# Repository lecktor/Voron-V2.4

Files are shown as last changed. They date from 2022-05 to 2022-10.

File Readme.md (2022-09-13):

# Voron V2.4R2 Kit by Lecktor

Lecktor.com sells full solution kit. To get a better understanding, please
take a look at our [manuals](./Manuals/Readme.md). For whats included in kit and why, take a look at mods like [NeverMore](./NeverMore/Readme.md), [EuclidProbe](./EuclidProbe/Readme.md), [Titanium Backers](./Backers/Readme.md), [Microswitch Endstop](./Microswitch_Endstop/Readme.md), [Door Hinges](./Door_Hinges/Readme.md) and other folders for more information. 

# Full BOM of kit
## Frame kit
- LDO Motors frame kit (black) - 1pcs

## Motor kit
- LDO Motors LDO-42STH48-2004AC (Z motor) - 4pcs
- LDO Motors LDO-42STH48-2004MAH (AB motor) - 2pcs
- LDO Motors LDO-36STH20-1004AHG (E motor) - 1pcs

## Linear rail kit
### Voron V2.4 250x250
- Linear rail LDO-SLR9H-300Z0 (stainless steel)  - 6pcs
- Linear rail LDO-SLR12H-300Z1 (stainless steel) - 1pcs
### Voron V2.4 300x300
- Linear rail LDO-SLR9H-350Z0 (stainless steel)  - 6pcs
- Linear rail LDO-SLR12H-350Z1 (stainless steel) - 1pcs
### Voron V2.4 350x350
- Linear rail LDO-SLR9H-400Z0 (stainless steel)  - 6pcs
- Linear rail LDO-SLR12H-400Z1 (stainless steel) - 1pcs

## Motion kit
- RainDew F695-2RS flanged bearing  (ABEC-7) - 20pcs
- RainDew 625-2RS ball bearing (ABEC-7) - 12pcs
- Runice pulley 16T/6mm/5mm (black) - 4pcs
- Runice pulley 20T/6mm/5mm (black) - 2pcs
- Runice pulley 20T/9mm/5mm (black) - 4pcs
- Runice pulley 80T/6mm/5mm (black) - 4pcs
- Runice idler 20T/6mm/5mm (black) - 2pcs
- Runice idler 20T/9mm/5mm (black) - 4pcs
- Gates Unitta belt loop 188-2GT-6RF - 4pcs
- Shaft 5x61mm - 4pcs
### Voron V2.4 250x250
- Gates Unitta timing belt LL-2GT-9RF (910mm)  - 4pcs
- Gates Unitta timing belt LL-2GT-6RF (1600mm) - 2pcs
### Voron V2.4 300x300
- Gates Unitta timing belt LL-2GT-9RF (1010mm) - 4pcs
- Gates Unitta timing belt LL-2GT-6RF (1800mm) - 2pcs
### Voron V2.4 350x350
- Gates Unitta timing belt LL-2GT-9RF (1110mm) - 4pcs
- Gates Unitta timing belt LL-2GT-6RF (2000mm) - 2pcs

## BuildPlate kit
### Voron V2.4 250x250
- LDO Motors spring steel sheet (textured; 254x254x0.5mm) - 1pcs
- Schallenkammer magnetic foil (graviflex; 255x255x1mm) - 1pcs
- Lecktor universal build plate (250x250x8mm) - 1pcs
- Keenovo heating pad (200x200mm; 500W/220V) - 1pcs
### Voron V2.4 300x300
- LDO Motors spring steel sheet (textured; 305x305x0.5mm) - 1pcs
- Schallenkammer magnetic foil (graviflex; 305x305x1mm) - 1pcs
- Lecktor universal build plate (300x300x8mm) - 1pcs
- Keenovo heating pad (240x240mm; 600W/220V) - 1pcs
### Voron V2.4 350x350
- LDO Motors spring steel sheet (textured; 355x355x0.4mm) - 1pcs
- Schallenkammer magnetic foil (graviflex; 355x355x1mm) - 1pcs
- Lecktor universal build plate (350x350x8mm) - 1pcs
- Keenovo heating pad (300x300mm; 750W/220V) - 1pcs

## Panels kit
- Lecktor (NeoBond 4mm/black; PMMA 3mm/clear) - 1pcs

## Chains set
### Voron V2.4 250x250
- Igus E2i.10.10.018.0 energy chain (16 links) - 2pcs
- Igus E2.15.10.028.0 energy chain (22 links) - 1pcs
### Voron V2.4 300x300
- Igus E2i.10.10.018.0 energy chain (19 links) - 2pcs
- Igus E2.15.10.028.0 energy chain (25 links) - 1pcs
### Voron V2.4 350x350
- Igus E2i.10.10.018.0 energy chain (22 links) - 2pcs
- Igus E2.15.10.028.0 energy chain (28 links) - 1pcs

## Electronics kit
- Fysetc Spider 446 V2.2 - 1pcs
- Fysetc TMC2209 V3.1 - 7pcs
- Fysetc Mini12864 RGB LCD V2.1 (type B) - 1pcs
- Raspberry PI 4 Model B (4Gb) - 1pcs
- Fisher Elektronik heatsink for Raspberry PI (ICK BGA; 14x14x10mm) - 1pcs
- 3M heat transfer tape (3M 8810; 15x15x0.25mm) - 1pcs
- Goodram 16Gb memmory card - 1pcs
- Sunon axial fan (MF60202V3-1000U-A99) - 2pcs
- Lecktor microswitch endstop module (black; PCB) - 1pcs
- Lecktor Z-endstop (black; PCB assembly) - 1pcs

## Power kit
- MeanWell RSP-200-24 PSU - 1pcs
- MeanWell RS-25-5 PSU - 1pcs
- Omron SSR G3NA-210B-UTU 5-24VDC - 1pcs
- SSR DIN rail mounting bracket (R99-12; black) - 1pcs
- ZF Electronics rocker switch DPST 16A (WRG32F2BBRLN) - 1pcs
- TE Connectivity power inlet 10EGG1-2 - 1pcs
- LittleFuse 0232004.MXP - 2pcs
- Logilink keystone CAT6 insert (shielded; NK4011) - 1pcs
- Logilink patch cord (black; 1m) - 1pcs
- ESPE IEC C13 power cable (black; 1.5m) - 1pcs
- Schneider Electric terminal block 2.5mm2 NSYTRV22 (grey) - 2pcs
- Schneider Electric terminal block 2.5mm2 NSYTRV22BL (blue) - 2pcs
- Schneider Electric terminal block 2.5mm2 NSYTRV22PE (ko-ro) - 2pcs
- Schneider Electric terminal cover 2.5mm2 NSYTRAC22 - 1pcs
- Schneider Electric bridge 2.5mm2 NSYTRAL22 - 3pcs
- OBO wiring box 40Kx25L LK4 40025 (gray; PVC) - 1pcs

## Wire harness kit
- Lecktor stealhburner wire harness (Heluflon; JST; Molex) - 1pcs
- Lecktor power line wire harness (Heluflon) - 1pcs
- Lecktor miscellaneous wire harness (Heluflon; JST; Molex) - 1pcs

## Toolhead kit
- Phaetus Dragon hotend (black; HF) - 1pcs
- Phaetus Dragon silicone sock (black) - 1pcs
- Phaetus heater cartridge (24V/50W) - 1pcs
- Phaetus thermistor cartridge (104NT-4-R025H42G) - 1pcs
- Bondtech drivegear kit 1.75/5.0 - 1pcs
- Bondtech shaft assembly - 1pcs
- Bondtech thumbscrew assembly - 1pcs
- RainDew ball bearing MR85ZZ - 2pcs
- GDSTime axial fan (4010; 24V) - 1pcs
- Delta Electronics blower fan (5015; 24V) - 1pcs
- Lecktor toolhead front (Dragon/CW2/Nylon/MJF; black) - 1pcs
- Lecktor toolhead rear (Dragon/CW2/Nylon/MJF; black) - 1pcs

## Hardware kit
- Lecktor hardware kit (black) - 1pcs
- LDO Motors Voron V2.4 t-nuts - 1pcs
- LDO Motors Voron V2.4R2 rubber feet - 4pcs
- Lecktor hammer head M3 nuts (100pcs) - 1pcs

## DIN rails
### Voron V2.4 250x250
- Lecktor DIN rail (35x7.5x368mm; zinc) - 2pcs
### Voron V2.4 300x300
- Lecktor DIN rail (35x7.5x418mm; zinc) - 2pcs
### Voron V2.4 350x350
- Lecktor DIN rail (35x7.5x468mm; zinc) - 2pcs

## Miscellaneous
- Misumi extrusion slot cover (black; 1m) - 1pcs
- Foam panel tape (1x5x2000mm) - 2pcs
- Foam panel tape (3x5x3000mm) - 2pcs
- 3M VHB 5952 (9x5.5x2500mm) - 1pcs
- Bowden coupler (black; 4mm) - 1pcs
- PTFE tube (black; 4x2x1000mm) - 1pcs
- Neodymium disc magnet (black; 6x3mm) - 10pcs
- KSS Wiring cable tie (Polyamide; 1.6x71mm; black) - 100pcs
- FIX&FASTEN cable tie (Polyamide; 2.5x150mm; black) - 100pcs
- Misumi HNTAJ5-3 nut - 10pcs
- Misumi HNTAJ5-5 nut - 10pcs
- Cable duct for rails - 4pcs
- Cable sleeves for bottom - 3pcs

## LED mounts
- BTF-Lightning SK6812 led strip (250-350mm) - 3pcs
- FIX&FASTEN led profile (9.30x16x250-350mm) - 3pcs
- LED mounts plastic parts (eSun ABS+; black) - 6pcs
- LED mounts wire harness - 1pcs

## Titanium backers
- Lecktor Titanium backers hardware kit - 1pcs
### Voron V2.4 250x250
- LWLW X-rail backer (Titanium grade 2; 2x18x260mm) - 2pcs
- LWLW Y-rail backer (Titanium grade 2; 3x18x290mm) - 1pcs
### Voron V2.4 300x300
- LWLW X-rail backer (Titanium grade 2; 2x18x310mm) - 2pcs
- LWLW Y-rail backer (Titanium grade 2; 3x18x340mm) - 1pcs
### Voron V2.4 350x350
- LWLW X-rail backer (Titanium grade 2; 2x18x360mm) - 2pcs
- LWLW Y-rail backer (Titanium grade 2; 3x18x390mm) - 1pcs

## Nevermore assembly
- Nevermore carbon bag - 1pcs
- Sunon blower fan (MF5015VX-00U-A99; 12V) - 2pcs
- Lecktor Nevermore hardware kit (black) - 1pcs
- Lecktor Nevermore wire harness (Heluflon; JST) - 1pcs
- Lecktor Nevermore plastic parts (ABS GF; black) - 1pcs

## Euclid probe assembly
- Lecktor Euclid PCB assembly - 1pcs  
~~Lecktor Euclid wire harness (Heluflon; JST) - 1pcs~~  
~~Lecktor Euclid plastic parts (ABS GF; black) - 1pcs~~  
  
## Voron V2.4R2 plastic parts
- Main functional parts (eSun ABS+; black) - 1pcs
- Accent functional parts (eSun ABS+; red/gold) - 1pcs
- Skirts (eSun ABS+; black/red/gold) - 1pcs
- All threaded inserts are installed

###### Tags: V2.4, 2.4, V2.4R2, V2.4 R2

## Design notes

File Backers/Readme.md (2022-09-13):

# Gantry Backing Plates

## The theory
Due to different thermal coefficients of linear expansion between steel (rails) and aluminum (extrusions), the Voron V2 gantry forms a sort of giant bimetal temperature sensor element. This causes a warping of the gantry as it heats up with increasing chamber temperature.

## The evidence
While exploring [frame expansion behavior](https://github.com/tanaes/whopping_Voron_mods/tree/main/docs/frame_expansion), a number of us were noticing empirical values several times what we'd predict simply due to linear expansion of the Z extrusions alone. Although plugging those empirical values in to the compensation code has given me great first layers, the difference from expectation was still bothering me. Maybe, I thought, there was some sort of warping happening? Checking out a table of thermal expansion coefficients, I saw that indeed aluminum expands quite a bit more than steel with temperature.

### Bottom X rail increases frame thermal compensation value

After some discussion on Discord, it appeared that people running the BOM double X rail, with an MGN9 rail on the front and bottom of the X extrusion, by and large seemed to be needing higher compensation values than those who only had a single X rail on the front face of the extrusion.

So I tried loosening the screws on the bottom X rail of my V2.4 350, and re-ran the thermal expansion measurment. Wouldn't you know it, my observed compensation factor went from around 2.8 to about 1.5:

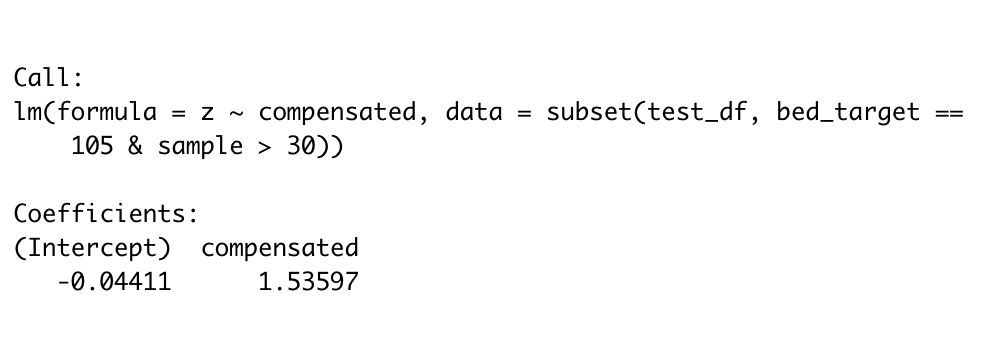
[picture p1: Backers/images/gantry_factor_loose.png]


### Bed mesh changes as predicted with frame temperature

To confirm, I decided to go ahead an loosen *all* the rails on both X and Y, heat soak the machine for a couple hours, and then tighten them down; this should ensure that the gantry is as flat as possible when at temperature, but will bow downwards when it is cold as the aluminum contracts more than the steel rail beneath.

And that's indeed what I saw. After hot-tightening the rails, I took a bed mesh while everything was still hot. I then allowed the printer to cool for a couple hours, reheated the bed, and took another mesh while the bed was hot but the frame was still cold.

What I saw was just what we'd predict, with the "hot frame" measurement (left) being quite flat, but the "cold frame" measurement appearing as if the center of the bed were closer to the probe:

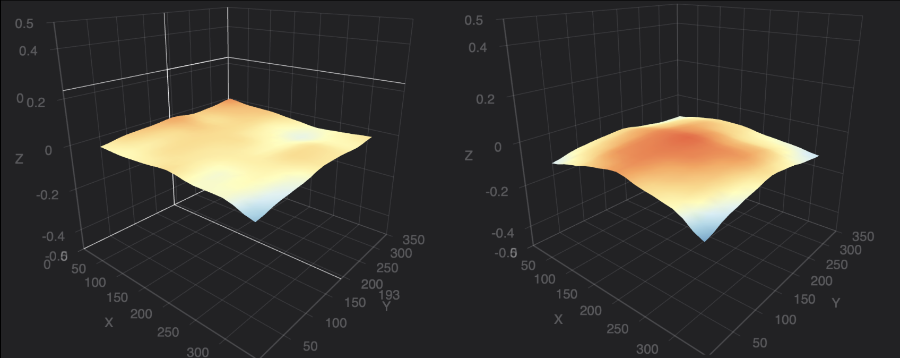
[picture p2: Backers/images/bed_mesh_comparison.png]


### Shitty modeling is consistent with observation

Finally, I put together a *very simplistic* FEA model in Fusion360. It did the thing with the bendy bendy:

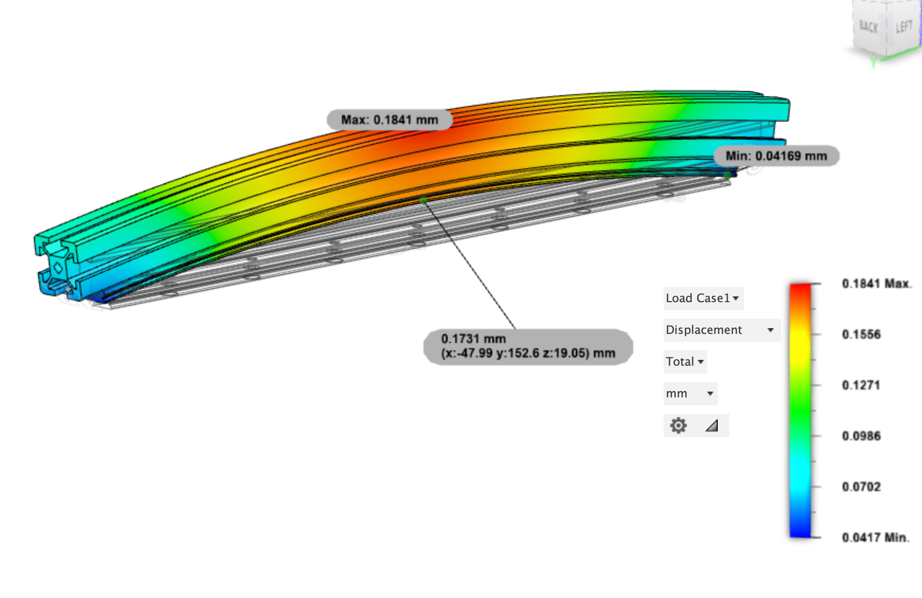
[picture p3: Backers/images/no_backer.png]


 ***Caveat: I am a biologist, not an engineer!*** I only barely know what I'm doing with this shit. But with the rail material set to 440C stainless and the extrusion to 6061 aluminum, with them bonded at the interface, a temperature delta of 40° C led to this 250mm-sized X gantry member deflecting 0.17 mm upwards in the center! That's definitely not trivial, and it's certainly consistent with our empirical observations.
 
## The (a) solution (maybe??)
 
Why have *bi*metal when you can have *tri*metal?!

At one extreme, bolting another MGN9 rail on top of the extrusion seems certain to cancel out the bending moment imparted by the one on the bottom. 

As a cheaper alternative, I've designed some laser-cut steel extrusion backing plates that weigh less and are lower-profile than rails, but which should at least do a reasonable job at counteracting the thermal defection.

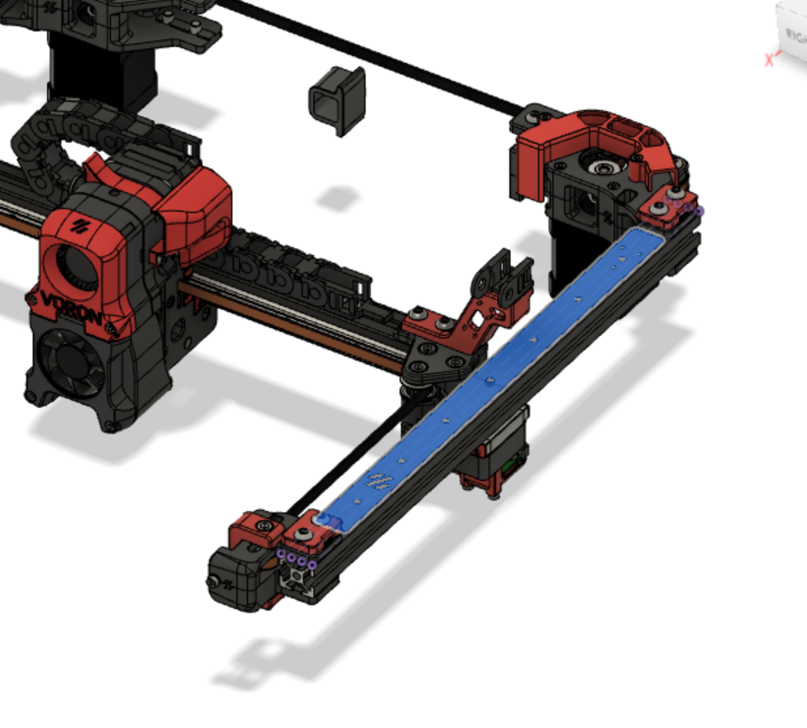
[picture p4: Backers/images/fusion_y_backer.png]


These are sized to fit along the top of the Y extrusion and on the top or back of the X extrusion, with a few mm of clearance to printed endpieces:

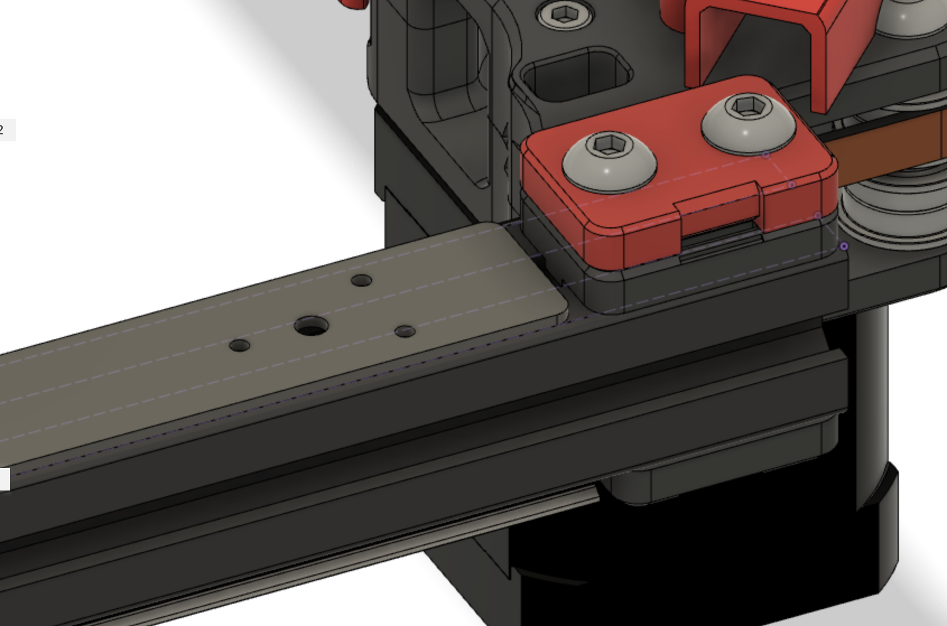
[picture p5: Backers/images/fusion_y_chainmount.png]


They also have pilot holes for the cable chain end link to attach. They are sized to be drilled out with a 2.5 mm bit and then M3 tapped. (Laser cutting hardens the steel at the cut, so the cut holes are undersized for drilling out to be a bit gentler on your taps.)

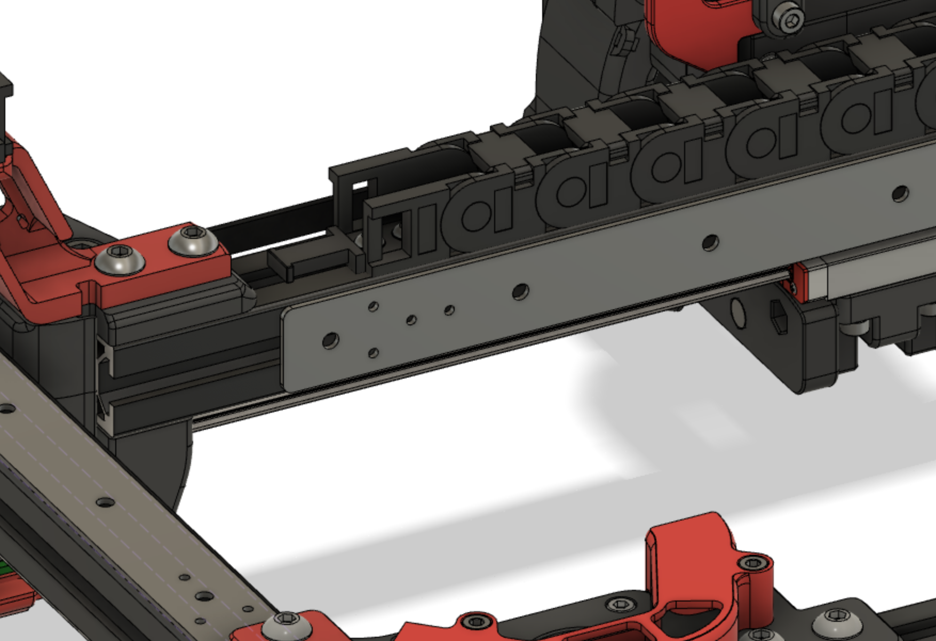
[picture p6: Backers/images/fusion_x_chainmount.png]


To attach them most optimally, you'll also need to countersink the holes so they can be installed with 6mm flat head M3 screws.

### Simulation results

Plugging these into the FEA model shows some serious improvements with a 1.9 mm steel backer:

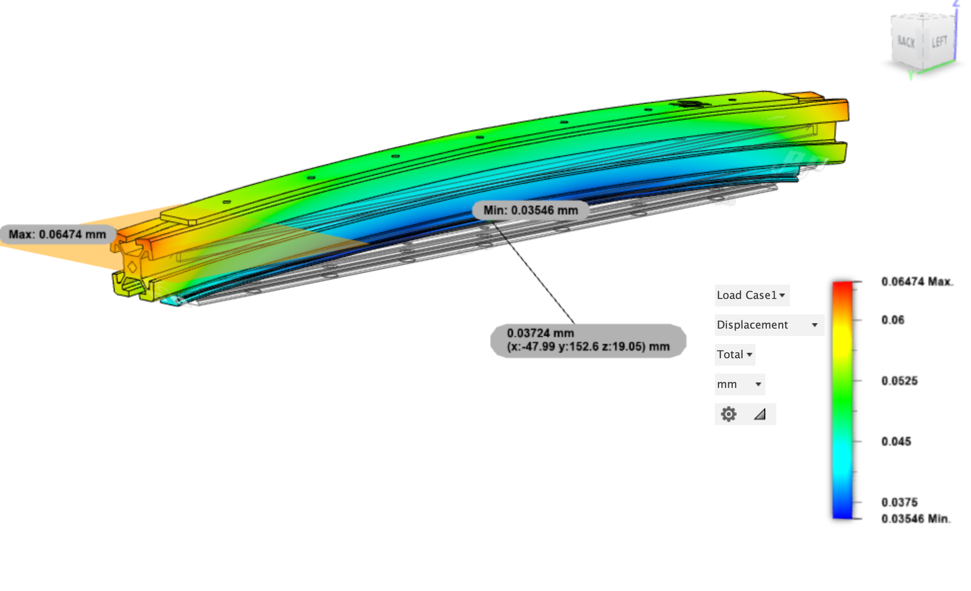
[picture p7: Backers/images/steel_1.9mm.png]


A 1.5 mm titanium backer does even better:

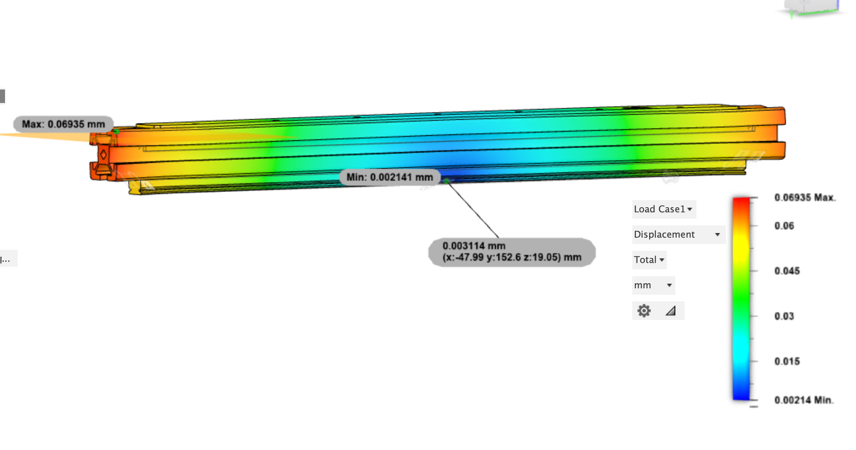
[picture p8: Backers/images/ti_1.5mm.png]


### Sourcing

A set of 3 backers in 1.9 mm steel can be bought at [SendCutSend](https://www.sendcutsend.com) for somewhere in the neighborhood of $10 (presuming you've met their minimum order of $29). 

If you're feeling spendy, even the Ti backers still cost about the same as cheapo linear rails, with a set of three costing around $60.

## The results

I put in an order for 8 sets of backers in various sizes, all of which have been sent out to people on the Voron Discord for testing. Most of these were in mild steel, but there are also a few pieces in titanium.

Results from testing are below.

### Case study 1: whoppingpochard, steel backers X and Y

After countersinking and tapping my mild steel backers, I tried hastily cold-bluing them with some gun blue. The results were decidedly mixed, and I *also* very conveniently misplaced my 3-in-1, so sadly they were a little splotchy the next morning. They installed perfectly on the machine, though, with apparently just enough clearance without modifying cable chains: 

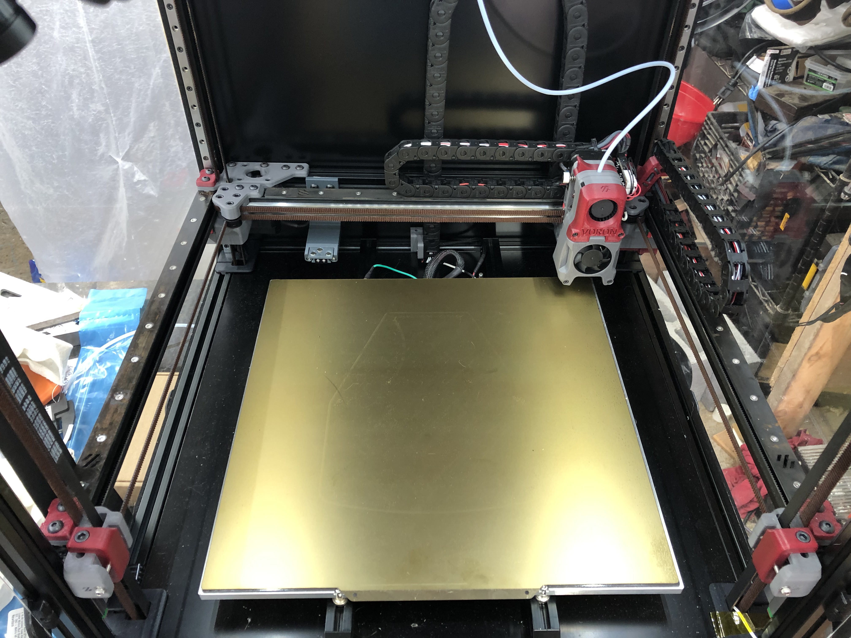
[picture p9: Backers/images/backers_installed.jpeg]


To test, I performed the following operation:
1. preheated the bed
2. took a bed mesh while bed was still hot
3. took a bed mesh after 2 hour heat soak (frame at ~35° C)
4. installed backers on each axis
5. repeated steps 1-3

This is the result:

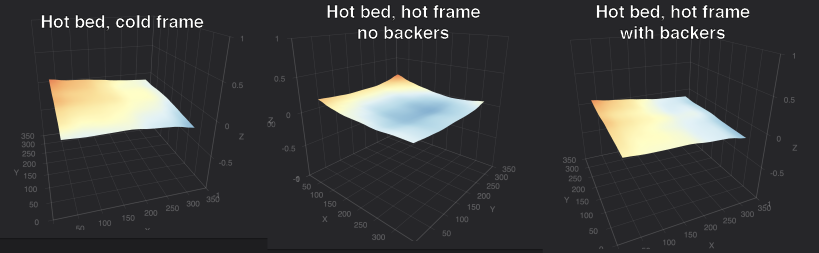
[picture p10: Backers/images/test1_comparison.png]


(Please ignore the odd tilt of the bed, as I think I did QGL at a non-equilibrium point.)

The hot bed appears pretty planar from the perspective of the toolhead while the frame is still cold. *Without* backers, after the frame has heatsoaked, the bed appears cupped -- presumably due to the extrusion bending upward towards the center. 

But *with* backers installed, the bed still appears planar after the heatsoak. This appears to indicate the backers are actually working!

I also developed a script to test gantry bowing in a more controlled fashion. Essentially, the script does a bed mesh while the frame is cold and then another once the frame heats up, and compares the two. As long as the bed is the same temperature for each mesh, we assume that any non-linear deviation measured is a result of flexing frame members.

Here are the results from my printer, with and without backers installed (I ran this test after swapping out the steel X backer for a titanium one):

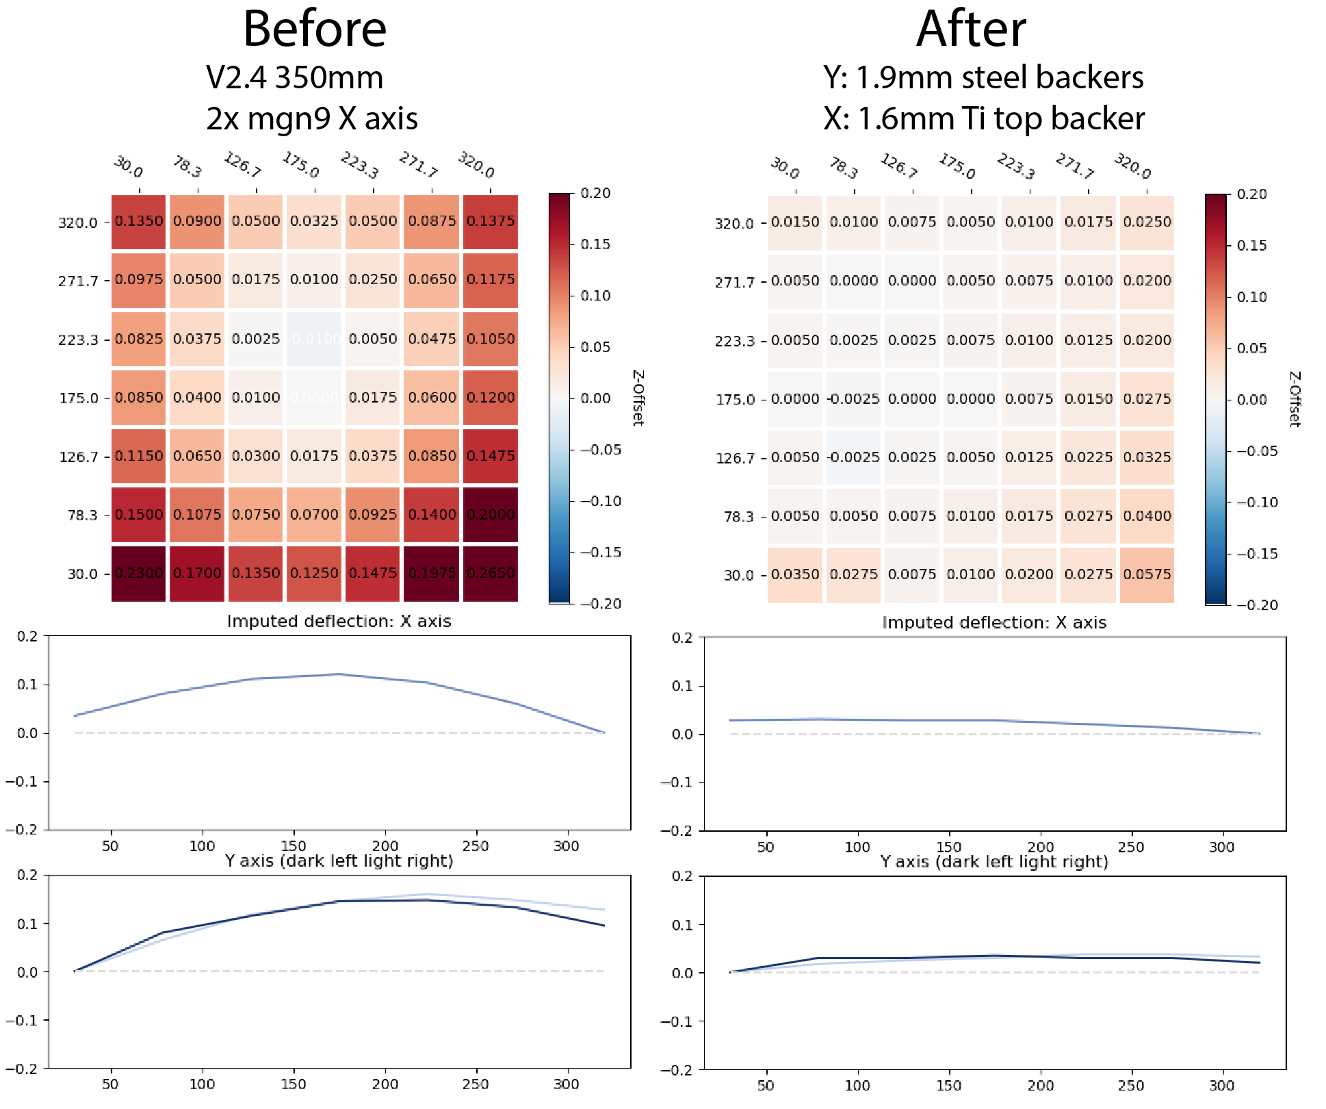
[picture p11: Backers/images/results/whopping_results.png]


The mesh heatmap is not a measure of the bed surface itself, but rather the *difference* between the hot-frame mesh and the cold-frame mesh. It shows that, on my printer, I get more than 0.25 mm of cumulative change over the span of my bed -- more than a whole first layer thickness!

The line plot is a rough approximation of how we are inferring the gantry frame members are flexing, based on the pre- and post-heat measurements. Although not perfect, it gives us an intuitive illustration of the effect.

On the right side, you can see that installing the backers improved my measurements substantially! The titanium backer on X may indeed be doing better than the *thicker* steel backers on Y.

### Case study 2: garretwp, V2.4 300 mm

In principle, the MGN12 X-axis mod should help ameliorate the bowing problem in X as the single rail is on the front of the X extrusion, thus should not induce any bowing in that extrusion along Z.

That is what garretwp finds with his V2.4 300mm, which is running MGN12 on X. 

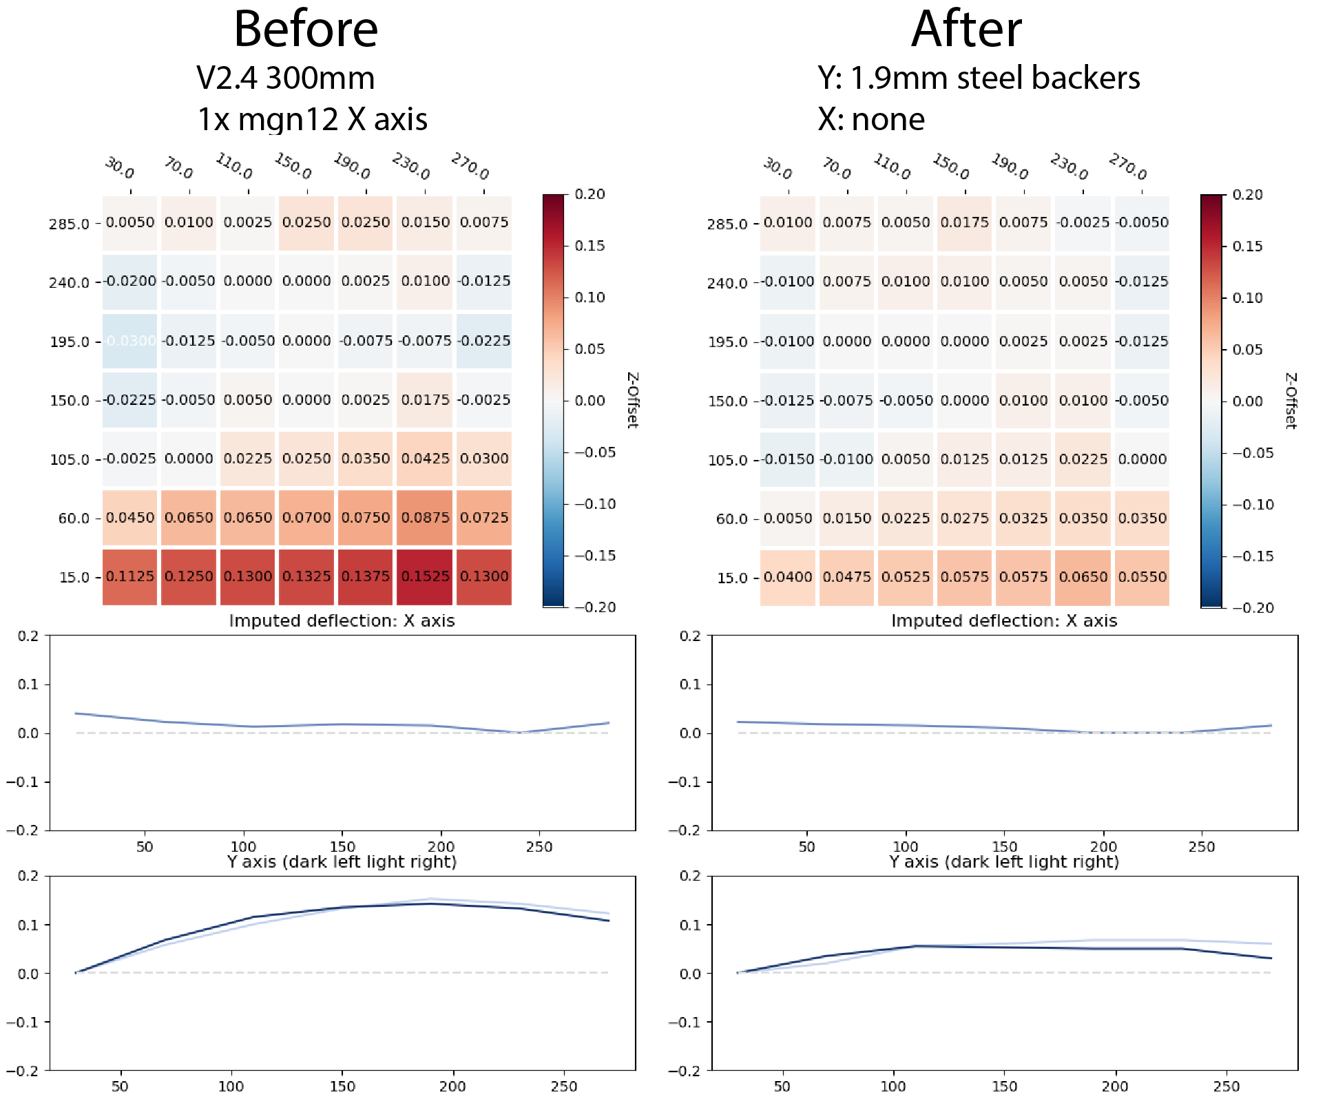
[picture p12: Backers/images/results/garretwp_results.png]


Before installing backers, he measures substantial deflection along Y, but little if any on X. After installing Y backers, the Y deflection is substantially reduced and X is unchanged.

### Case study 3: mgn9 rail as extrusion backer

bythorsthunder and BnE both are running V2.4 350mm machines with the MGN12 X-axis mod. 

bythorsthunder had his original mgn9 X-axis rails laying around, and installed them on top of the Y axis extrusions to offset bowing induced by the bottom rails.

BnE installed steel backers on Y.

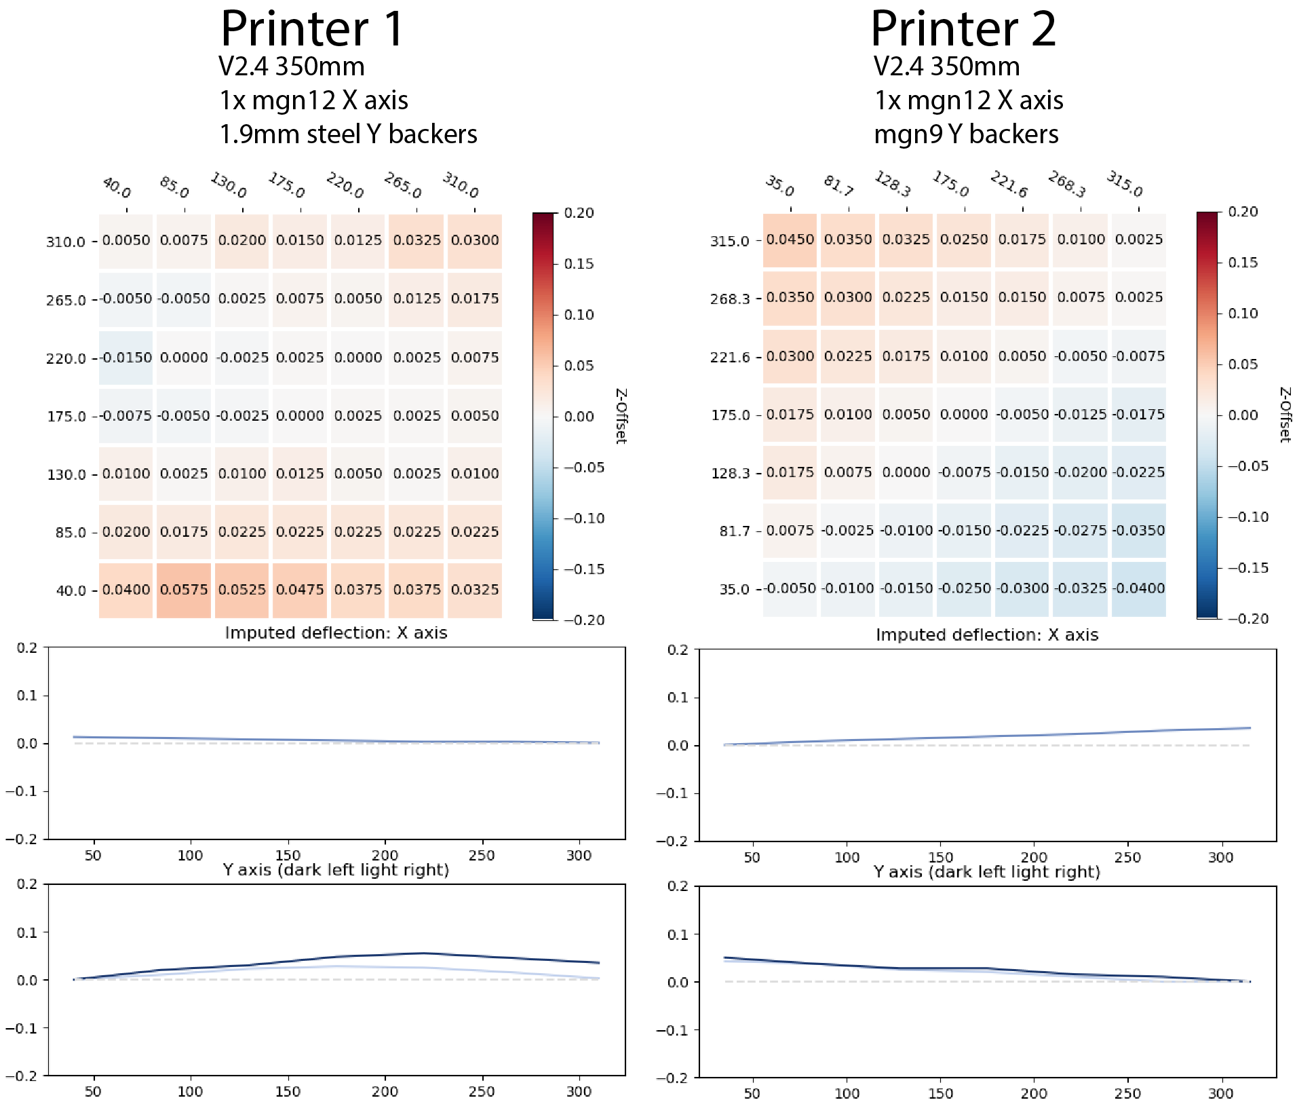
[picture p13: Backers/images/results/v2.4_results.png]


In both cases, we see very straight X axes and little deflection along Y. Although there's some as-yet unexplained overall tilt apparent in bythorsthunder's run, there is absolutely no apparent curve along Y -- indicating that the mgn9s on top of the extrusion *perfectly* offset the rails on the bottom. Although using rails as extrusion backers requires a bit of reconfiguring (especially if running cable chains), they look like a mechanically perfect solution, especially for Y where the added mass is less of a concern.

### Case study 4: V1.8s

The rail arrangement on V1s differs from on V2s, as the Y rails are on top rather than bottom of the extrusion.

In cassiespook's v1.8 (left), we can see the resulting deflection results in a sort of saddle shape, with X bowing upwards and Y downwards. 

Yeri is running a single MGN12 on X, and although there is also some unexplained overall tilt apparent in the delta cold/hot mesh, we do see that X seems to be unbowed in Z, as we saw with the MGN12 V2s.

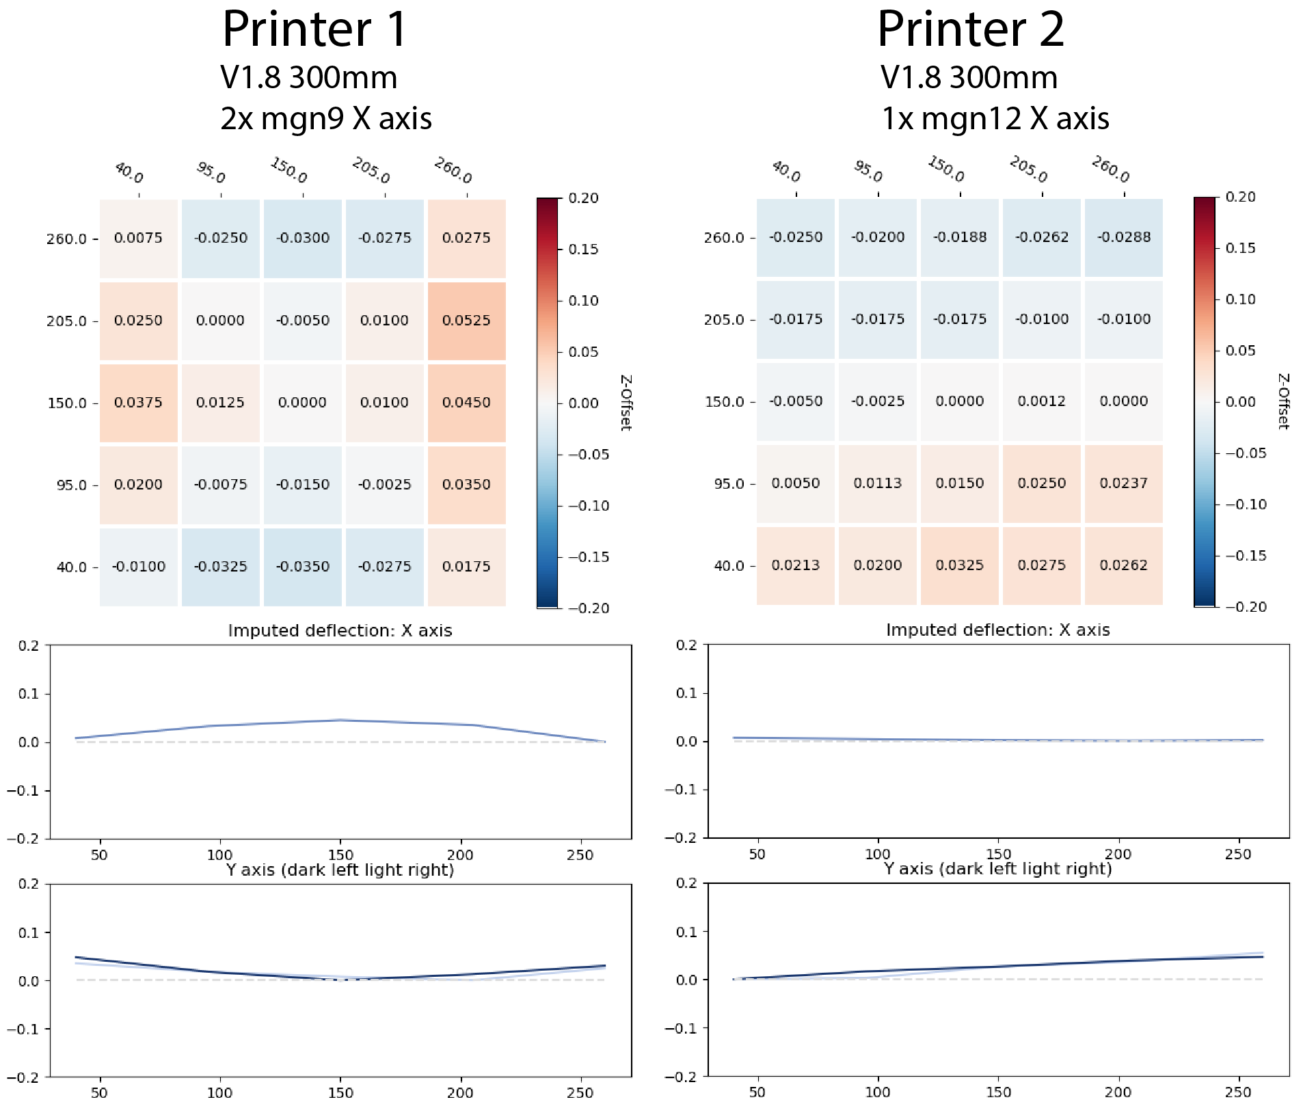
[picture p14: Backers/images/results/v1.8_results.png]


---
### Back: [Voron V2.4R2 kit by Lecktor](../Readme.md)

# Sources:
[whoppingpochard extrusion backers Github](https://github.com/VoronDesign/VoronUsers/tree/master/printer_mods/whoppingpochard/extrusion_backers )

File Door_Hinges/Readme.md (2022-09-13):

# Voron 2.4 Hinge Mod for 3mm Doors with 3mm Foam
This is designed for 3mm door panels with 3mm of foam. I used the laser cut panels from [Printed Solid](https://www.printedsolid.com/collections/voron-collection/products/voron-v2-clear-acrylic-sheets-for-sides) which are 3.175 (1/8") and the foam tape from [Amazon](https://www.amazon.com/gp/product/B07QYGN3C1). They are design to fit Misumi extrusions. If the width of your extrusion is not the same, you can adjust the part that goes into the extrusion.

Make sure the panels you use are cut to specifications. 0.5mm too large on each panel can cause issues. Also, make sure you flow rate is dialed in. There isn't much room in the design for overextrusion.

The M3x40mm bolt used as a pin is designed to fit tight in the hinge. It will pivot when the door is opened/closed so don't tighten it too far in the insert below. You will need to thread the bolt in the top part of the hinge and when your bolt hits the non-threaded part (assuming your bolts are not 100% threaded) you will need to pursuade it thru the hinge pivot block. Once thru, I would back it out and go back in a couple times.

If you are over extruding, you will have difficulty getting the bolt into the hinge. Feel free to use the step file to open the hole up if you need to. I did not want any play in the hinge.

I recommend drilling the holes in the panel with a 4mm or 5/32" bit made for acrylic. If you do not have an acrylic bit available, please find some guides and/or watch some videos on how to successfully drill your panel. If you have scrap arcylic, please try it first. Having a hole a little larger than the bolt will provide some "wiggle" room. You can loosen the bolt, move the panel a little and tighen back up. The edge of the panel might catch on the bolt that goes into the extrusion, so some filing may be needed. (See Photo 1/2)

The backplate on the hinge helps spread the load and prevents cracking of the panels. You do not need to use them if you have shorter bolts and don't want to use them. I would, however, recommend using them. The handles do not have backplates. As long as you do not overtighten them, they should be fine. Use some button heads if you can. I didn't have any, and found socket heads work just as well.

There is not much space behind the inserts on the hinge. Be careful and do not press them too deep. Press them "almost" in and then use something like a straight edge to press them flush. It is easy to dimple the front side, especially if you use too long of bolts. (See Image 4 below).

Final note: The pivot has a little "ear" that overhangs the other side of the extrusion. This is ensure the pivot is solid and fits square against the extrusion. It does mean that that you will not have foam on that part. (See Photo 2)

Handles
|item | qty |
|---|---|
|M3x6 BHCS  | x8 |
|M3 inserts | x8 |

Hinges
|item | qty |
|---|---|
|M3x40		| x4 (hinge "pin") |
|M3x12 SHCS	| x4 attaches pivot to frame |
|M3x10 BHCS | x8 attaches hinge to door panel |
|M3 inserts | x12 |

Image 1:

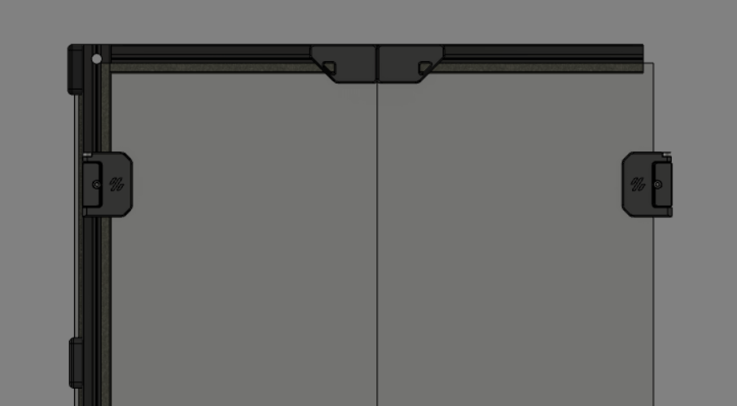
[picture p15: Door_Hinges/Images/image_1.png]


Image 2:

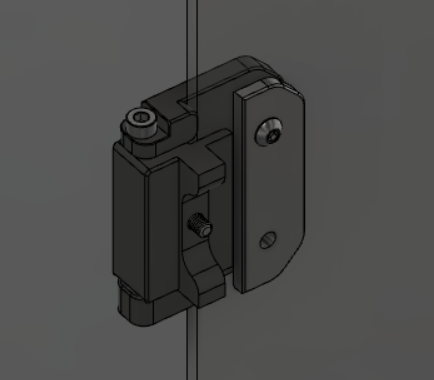
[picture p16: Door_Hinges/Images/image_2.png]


Image 3:

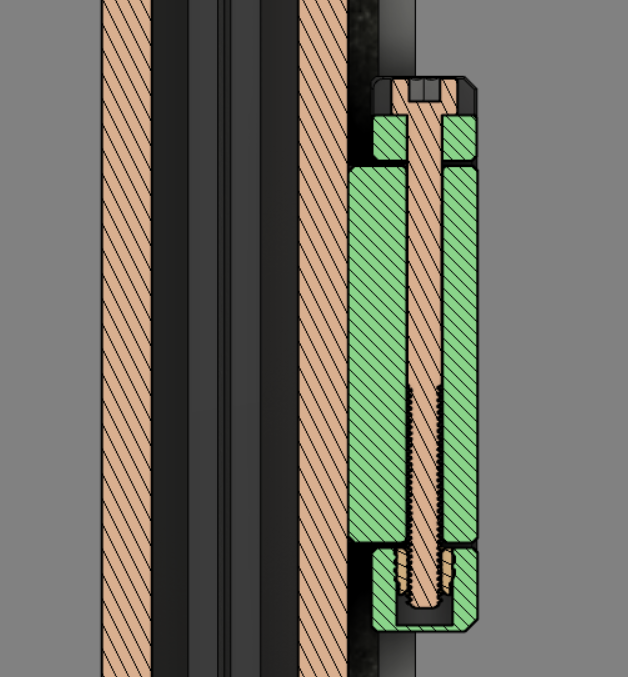
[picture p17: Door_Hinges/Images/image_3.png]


Image 4:

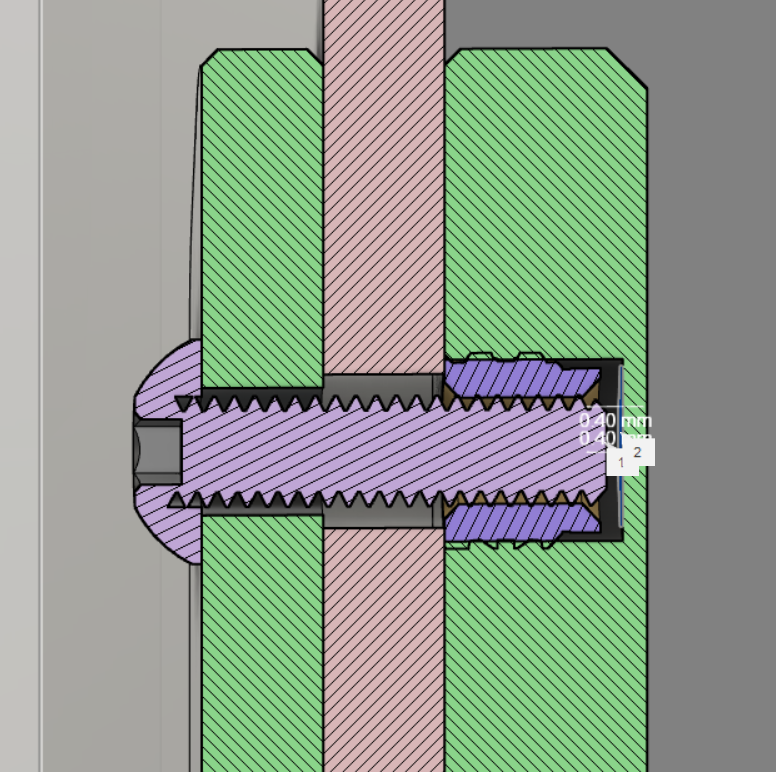
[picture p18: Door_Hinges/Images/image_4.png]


Photo 1:

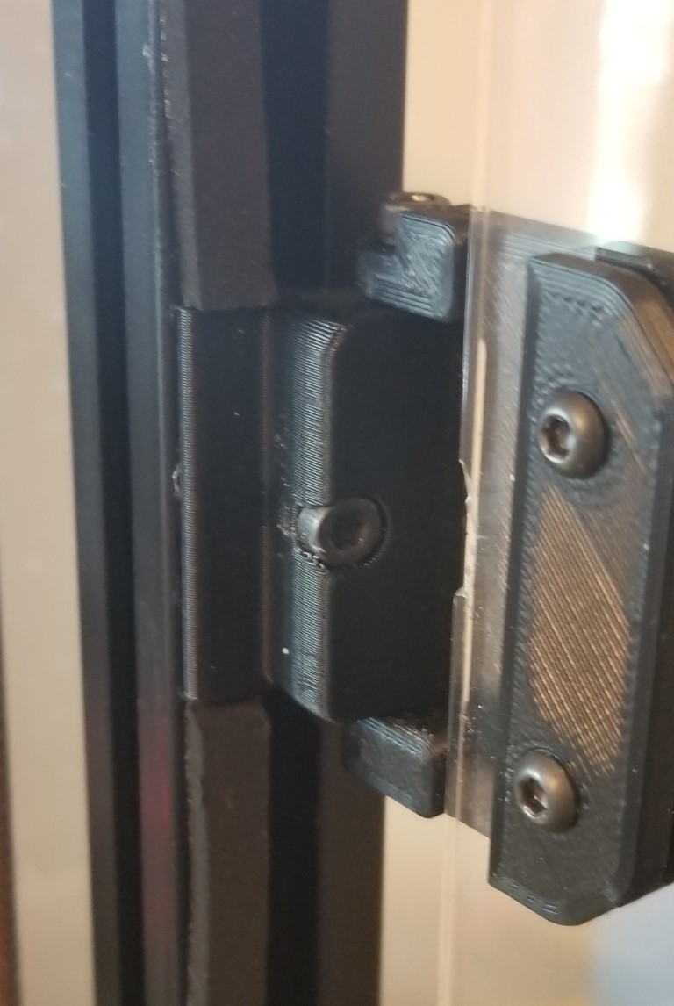
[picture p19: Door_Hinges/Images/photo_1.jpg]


Photo 2:

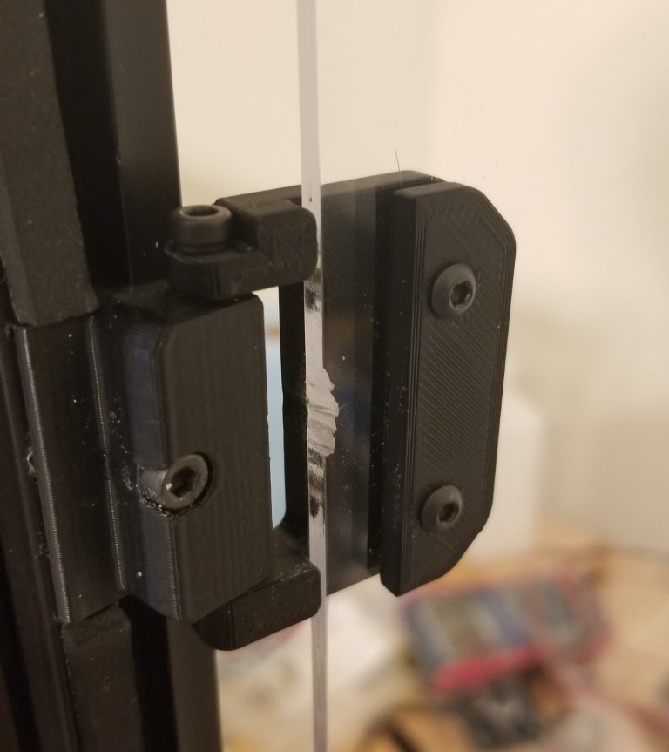
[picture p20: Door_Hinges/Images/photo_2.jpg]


Photo 3:

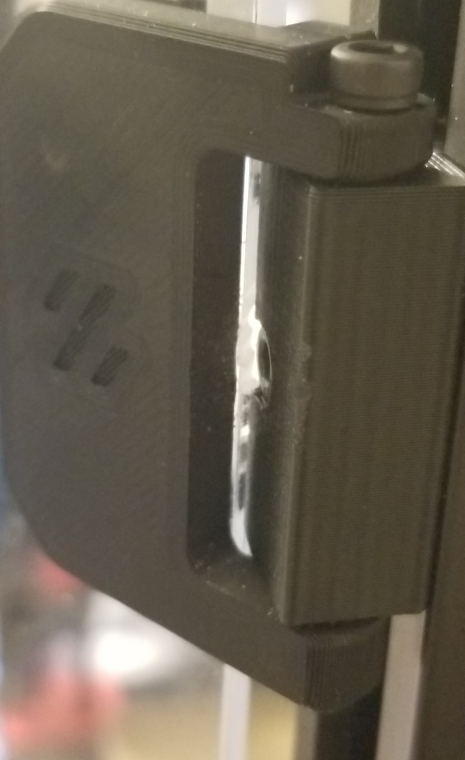
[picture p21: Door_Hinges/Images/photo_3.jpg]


Photo 4:

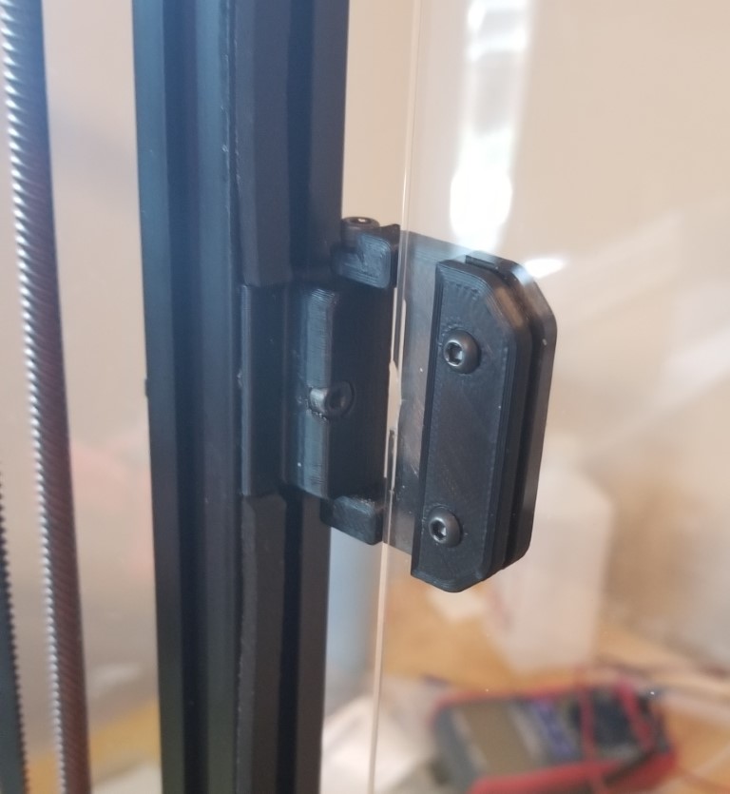
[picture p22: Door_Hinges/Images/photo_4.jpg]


Photo 5:

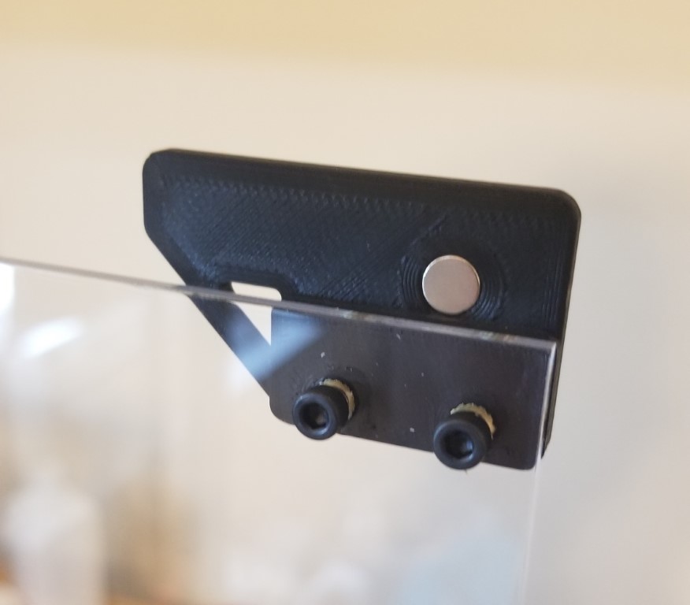
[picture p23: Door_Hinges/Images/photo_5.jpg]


Photo 6:

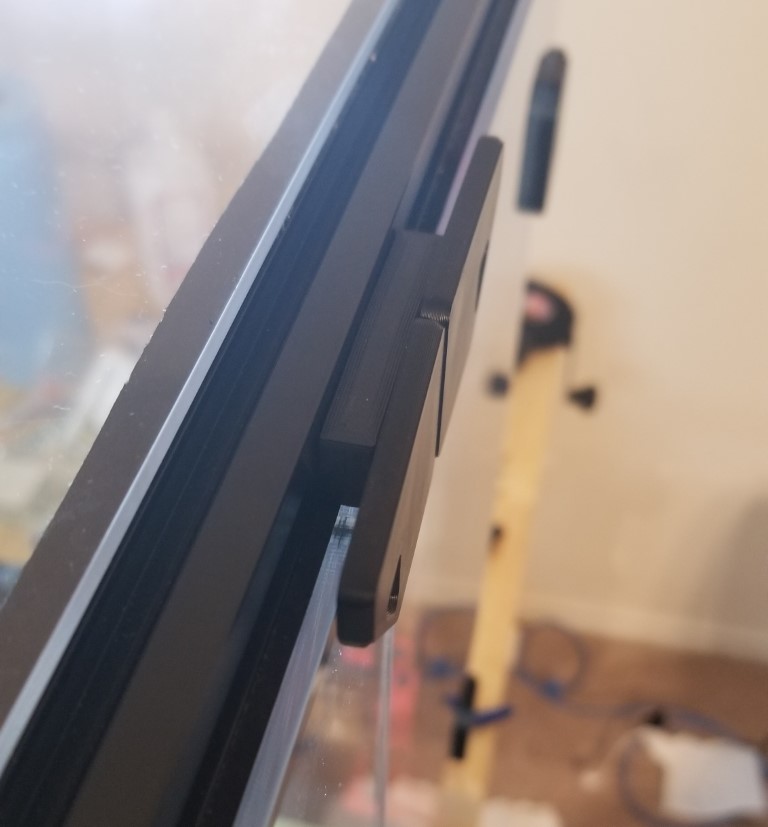
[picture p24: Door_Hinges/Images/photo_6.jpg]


Photo 7:



---
### Back: [Voron V2.4R2 kit by Lecktor](../Readme.md)

# Sources:
[randell Door Hinges Github](https://github.com/VoronDesign/VoronUsers/tree/master/printer_mods/randell/Door_Hinges)

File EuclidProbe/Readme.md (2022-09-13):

# EUCLID PROBE
The highly accurate, magneticaly coupled Z-Probe that is not affected by bed temp, bed material, magnetism or surface treatment.

The probe can be configured to be used as Z-endstop, be manually or automatically deployed via gcode macros, and can take advantage of the firmware's probe pickup detection scheme to ensure pickup/release. It uses screw attached magnets for both mechanical coupling and for electrical contact. The Z-Probe circuit is completed when the probe is attached.

The unique dock design securely captures the probe, providing secure and reliable docking and undocking.

[Rest of documentation](https://www.euclidprobe.com)

---
### Back: [Voron V2.4R2 kit by Lecktor](../Readme.md)

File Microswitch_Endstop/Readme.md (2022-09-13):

# Voron 2.4 XY Microswitch Endstop for PCB
POD for use with the Microswitch endstop pcb board for X and Y axes.

Check [Microswitch_Endstop](https://github.com/VoronDesign/Voron-Hardware/tree/master/Microswitch_Endstop) for the microswitch pcb.

Installed
Mounted 1 Mounted 2
Mounted 2 Mounted 3

---
### Back: [Voron V2.4R2 kit by Lecktor](../Readme.md)

# Sources:
[randell Mircoswitch Endstop Github](https://github.com/VoronDesign/VoronUsers/tree/master/printer_mods/randell/Microswitch_Endstop)

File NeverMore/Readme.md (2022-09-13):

# Nevermore Activated Carbon Filters - Micro Edition

<div align="center">Nevermore Micro V5 Duo (dual fan)</div>

Nevermore Activated Carbon Filter Micro V5 Duo

Originally intended as a carbon fume filter for Voron V2, it has found its way into a multitude of other machines. Let yours be the next! Bad smells or fumes, or complaints thereof, should not keep you from being a maker!

- [Nevermore Activated Carbon Filters - Micro Edition](#nevermore-activated-carbon-filters---micro-edition)
- [About The Nevermore Micro](#about-the-nevermore-micro)
  - [Why The Nevermore?](#why-the-nevermore)
  - [Nevermore Background](#nevermore-background)
  - [Nevermore V5 Duo](#nevermore-v5-duo)
- [FAQs](#faqs)
  - [What fans should I use?](#what-fans-should-i-use)
  - [How do I make a suggestion/report a bug/find out more?](#how-do-i-make-a-suggestionreport-a-bugfind-out-more)
- [Getting Started](#getting-started)
  - [SOURCING THE PROPER ACID-FREE CARBON](#sourcing-the-proper-acid-free-carbon)
  - [NEVERMORE 3D PRINTER CARBON](#nevermore-3d-printer-carbon)
  - [BOM (V5)](#bom-v5)
  - [Assembly](#assembly)
    - [Instructions for V5](#instructions-for-v5)
    - [Instructions for V4](#instructions-for-v4)
  - [Final Thoughts on Usage](#final-thoughts-on-usage)
    - [Back: Voron V2.4R2 kit by Lecktor](#back-voron-v24r2-kit-by-lecktor)
- [Sources:](#sources)

# About The Nevermore Micro

[VOCs (Volatile Organic Compounds)](https://en.wikipedia.org/wiki/Volatile_organic_compound) are common in daily life but VOCs generated from 3D printing are known to cause severe health issues and even cause cancer in some cases.

Emitted VOCs

A study from 2013 of [ultrafine particle emissions from desktop 3D printers (2013)](https://www.sciencedirect.com/science/article/pii/S1352231013005086) is a good start to understand the importance of your filament choices and the printer's environment.

Characterization of volatile organic compound emissions from consumer level material extrusion 3D printers (2019)
_(credit: [Characterization of volatile organic compound emissions from consumer level material extrusion 3D printers (2019)](https://www.sciencedirect.com/science/article/pii/S0360132319304196))_

Characterization of particulate and gaseous pollutants emitted during operation of a desktop 3D printer (2019)
_(credit: [Characterization of particulate and gaseous pollutants emitted during operation of a desktop 3D printer (2019)](https://www.sciencedirect.com/science/article/pii/S0160412018323663))_

## Why The Nevermore?

At the end of the day, a fresh single-pass filtered exhaust (at brand new) has perhaps 70% VOC removal efficiency while still exhausting 30% of the nasty. A worn-in 50% efficiency recirculation filter achieving four passes would still remove 94% of the bad stuff. Or 99% at six passes!

The number of passes you get all depends on how well you can seal your build chamber.

Some will have a hard time achieving a good chamber seal, which creates the biggest drawback of recirculation filters - _they're air flow neutral_. Meaning, as nothing pulls air into the chamber, air can diffuse freely to the outside through any remaining gaps. And that air could be _zero-per-cent_ cleaned...

If you plan on using only a Nevermore - be sure to seal your chamber as good as possible to prevent diffusing.

## Nevermore Background

There are many options for 3d printing air filters. Here’s a short list, and why I eventually settled on creating Nevermore:

**1. Home air purifiers**

**PRO:** Plug and play! High air flow (mostly). Will filter most particles a 3d printer produces.

**CON:** ABS headaches are not from particles, but Volatile Organic Compounds (VOCs), that are two orders of magnitude smaller than any particles a HEPA or ULPA could trap - they’re essentially gasses.

While home purifiers typically also contains carbon filtration and/or photocatlytic UV filtration stages, they will still not be suitable for 3d printing. Why? Efficient carbon adsorption in sufficient amount and stages is an absolute airflow killer, so most purifiers contain only a thin layer of carbon mesh/pellets that will be fully adsorbed within days or weeks at full power. And even if the filter is not used, contact with air saturates the carbon in 1-2 months. Yet they’re advertised as lasting for 6 months – that's only true for the HEPA component, not the VOC adsorbant carbon we're after.

And replacement filters typically run 20-60 USD a pop. Quite a lot for changing every few weeks when the carbon component depletes.

UV photocatalyst activity can last though; however, breakdown is slow and inefficient with voc halflives of several hours. The TiO2 layer reacting to the UV will also easily get irreversibly blocked by silicates (of which there are a lot in peoples homes, in everything from sink and bathroom sealants to plaster walls). And breakdown will many times be incomplete. Styrene passing a PCO filter might get turned to even more dangerous benzene, for instance.

**2. Carbon/HEPA filter combinations like the Zortrax M Series HEPA Filters**

Same as above. The HEPA component will keep working, but the carbon is just a few pebbles per hex. It could provide partial VOC clearance when fresh, but will quickly deplete with air flow. Then you need to replace it for 36 USD after a week of printing.

**3. Wet scrubber**

Awesome for both particles and VOCs, but its an industrial solution with any smaller home versions plagued by loud noise, water leakage and mechanical issues. It's not a solution for the masses.

**So, how about Nevermore?**

Well, the carbon in those filters mentioned above, costing a lot for little duration is actually dirt cheap. Whereas you get 20 grams for 36 USD with a zortax filter, **you can get 5000 grams for 36 USD in bulk**.

And with an enclosed chamber, you don't need the air flow of a room-size air purifier. Even a 350mm V2 Voron only holds about 5cf, meaning even a partial flow from a 5015 fan of 0.5-2cfm is enough to filter the fumes efficiently at the source.

So what are we waiting for? We got lots of cheap carbon. We can replace is easily. We don't need high airflow to clean a small chamber. We deal with poor efficiency of one-pass carbon filters by multiplying the amount and recirculate the air.

Enter, _The Nevermore_.

## Nevermore V5 Duo

Following the V4, the V5 Duo was released that changes the direction of air flow, better suited for when the Nevermore Micro would be placed flat on the bottom or top of the printer. Though there are other "outlet" options, like for the V1.8/Trident style that blows outwards and not up.

The V5 Duo also adds a 2nd additional 5015.

Nevermore Micro V5 Duo

Nevermore Micro V5 Duo

_(Nevermore V5 Duo. used with permission from Tightwad(JT)#6055)_

This repository hosts both versions, as they the same in design and function.

# FAQs
## What fans should I use?

Aim for any 5015 blower with a rating above 200Pa / 20mmH2O / 1 inH2O.

Since the fan (probably) cant be reused for other projects and will function in a high temp environment affecting its lifetime, go for budget. The Sunon Maglev MF50151VX (12V) / MF50152VX (24V) (high speed version, 6000 rpm) is good but unfortunately almost impossible to find as most are fakes. The GDStime 6000rpm Dual Ball bearing is another good option, but quality may vary. The Delta BFB0524HH is a gucci option, as is the special micro versions made for the papst rlf-35 which is an equally awesome and expensive fan. Any fan that works well for stealthburner should be a good option for nevermore micro as well.

See the BOM below for more details.

## How do I make a suggestion/report a bug/find out more?

- [The Nevermore Micro](https://github.com/nevermore3d/Nevermore_Micro)
  - [Report a Bug](https://github.com/nevermore3d/Nevermore_Micro/issues)
  - [Request a Feature](https://github.com/nevermore3d/Nevermore_Micro/issues)
- [Explore all Nevermore Activated Carbon Filters](https://github.com/nevermore3d)

# Getting Started

You're ready to build a Nevermore Micro? Cool!

> **_NOTE:_** MADE FOR ABS/PC/PETG - USE A DECENTLY HEAT RESISTANT FILAMENT !!

> **_NOTE:_**: Since you are committing to fan dissection, be aware a 5015 used for a NM Micro will most likely never find a different purpose!

## SOURCING THE PROPER ACID-FREE CARBON

**IMPORTANT!** Since first release the varying quality carbon out there has become increasingly evident. Users has both gotten bad carbon as well as outright dangerous stuff (in one case oxidizing most metal surfaces in a new voron in minutes. Be sure to vet your carbon supplier! You do not want your printer to look like this.

Acid residue on end-stop switch oxidizing

_(z end-stop switch after using acid residue carbon for 30 minutes, oxidizing)_

Acid residue on rails and screws oxidizing

_(oxidation on rails and screws after using acid residue carbon. used with permission from Zeptron#8880)_

Acid residue on filament tension spring oxidizing

_(oxidation on filament tension spring after using acid residue carbon. used with permission from Zeptron#8880)_

Acid residue on bolts and washers oxidizing

_(oxidation on bolts and washers after using acid residue carbon. used with permission from Zeptron#8880)_

Optimal carbon for 3D printer VOC adsorption is sourced from **virgin coconut**, not wood/bitumen/charcoal/bamboo/lignin/etc. The porosity for each and every source will vary greatly.

For example, for aquarium or moonshine use you want large macroporosity to filter larger impurities, like oils. For that reason, water/liquid-use carbon has a large macropore area, defined as >100nm. 3D Printer VOCs are generally less than 0.5 nm, meaning that **for optimal capture rate and efficiency we want carbon with a high microporosity ratio, defined as <1nm**. A higher iodine count >1000 usually indicates at least some micro/mesoporosity, and a higher hardness (>95%) will create less dust in air filtration. CTC number doesn't translate well to our VOCs; however, toluene adsorption - which sometimes is available - is a good metric.

**Avoid acid washed carbon at all costs**. Residues have oxidized printers! Go for steam activated, non acid-washed. A blend of neutral carbon and alkaline KOH carbon might be the best blend in the future, but impossible to currently source from trustworthy manufacturers.

Finding carbon that fills all criteria is hard. Look around, ask suppliers about the carbon, hear what others recommend. 

## NEVERMORE 3D PRINTER CARBON
**Nevermore offers its own premium carbon of unmatched specifications through selected voron resellers.** Its the best activated carbon for 3D printer use we have found after speaking to most major, vetted suppliers, offering benzene adsorbtion of up to 48 wt%, surface area of 1250 and CTC value of 80. It doesn't come cheap compared to bulk carbon from amazon, but its safe, has unbeatable performance, and every purchase supports the nevermore project by at least a dollar, see [Lecktor listing](https://lecktor.com/en/nevermore/870-nevermore-carbon.html)

## BOM (V5)

- 2x 5015 blowers (rating above 200Pa / 20mmH2O / 1 inH2O)
  - Sunon Maglev MF5015VX (high speed version, 6000 rpm. NOTE: There are A LOT of fake sunons out there, even from usually reputable sources. Blantant examples include 24V versions. Also, Sunon does not officially reecommend PWM:ing this fan, so while its still perfectly doable it can have unintended consequences later on) (There is no 24V version for this fan only comes in 12 V)
  - GDStime 6000rpm Dual Ball bearing on Aliexpress (This is 12V rated fans)
  - Delta BFB0524HH (This is 24V rated fans)
  - Avoid mechatronics fans for this purpose.
- 5x M3x0.5mm Heatset inserts (standard voron issue)
  - 2 for seating plenum to base
  - 2 for seating plenum lid to plenum
- 8x 6x3mm cylindrical magnets
- 1x 2 pin JST header
- 4x M3x16 BHCS
  - for heat inserts that go into the four fan tabs
- 1x M3x18 BHCS
  - ONLY for delta and v1.8 variants
- 1x M3x6 BHCS
- 1x M3x4 BHCS
  - for the extra hole in the plenum@lid for symmetry (it doesn’t attach to anything and is totally optional)

Acid-free Activated Carbon

- 4mm Active Carbon Air Filter Pellets

Optional for the cartridge closure

- 1x M3x0.5mm Heatset inserts
- 1x M3x6 BHCS

Optional for Vorons or any printer with 2020 extrusions

- 2x M3x12 SHCS
- 2x M3 2020 T-Nuts

Optional for Vorons or any printer using 24PSU
- 24 to 12 buck converter

## Assembly

Check out assembly images (**take note at how the fans are cut!**) here: [Nevermore V5 Plenum Assembly Album](https://ibb.co/album/0BN405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)

### Instructions for V5

_Coming soon... Similar to V4 though._

### Instructions for V4

Start by cutting up the 5015 so just the center remains. Take off the top half, cut the bottom piece circular along the fan blades. We aim for removing the focused air stream and instead achieve an even pressure across all of the filter medium.

The Nevermore Micro has three main parts: **Base**, **Plenum**, and **Cartridge** (plus lids for the plenum/cartridge).

- **Base** is mounted in the 130mm space between the bottom extrusions found on many vorons (designed for v2 originally). It’s seated with one m3 on each side, that screws into to a receiving 2020 M3 T-nut.

- **Plenum** holds the cut up 5015 fan, and is seated with two m3 screws into the base (base has two recieving m3 4mm heat inserts) on each side.

- **Cartridge** holds the filter medium of your choice (made for 4mm air filter active carbon pellets, but feel free to filter with what you think works best!). It snaps onto the Plenum piece for easy and quick removal.

For wiring, you are free to connect however works with your printer. If you do not have any direct controls on your MCU (controller board), then directly wiring may be your only option (with an inline switch).

However, if your MCU does have an additional fan output, then it is recommended to connect to it. If you are using Klipper on a Raspberry Pi, you have the option of using PWM fans and connecting the control wire to one of your PWM outputs on the RPi 40-pin header.

## Final Thoughts on Usage

**PID tune AGAIN if a Nevermore Micro is installed right beneath a heated bed, or draws/exhausts air over the bed thermistor. This is important, as worst case it could cause the bed to overheat, and/or make the heater adhesive burn (this will smell worse than any ABS printing!), and/or possibly even damage the bed heater.**

The Nevermore Micro's activated carbon will not filter Ultra-Fine Particulates (UFP). This is what the HEPA filter does in the Nevermore Mini (not released yet) and [Nevermore Max](https://github.com/nevermore3d/Nevermore_Max) variants. Those also have built-in negative-pressure fans.

However, you can achieve the same results with the Nevermore Micro by using a HEPA filter of your own and creating slightly negative air-pressure within your build chamber, exhausting air outwards at a slow pace. Since you are filtering with the Nevermore, the vast majority of VOCs will be filters by the active carbon filtration, leaving the HEPA filter to capture the remaining UFPs. This also greatly extends the live of your HEPA filter as the Nevermore Micro will be accumulating the larger particulates.

To create a negative pressure within your build chamber, simply install a fan to slowly draw air out of your build chamber and our through a HEPA filter. Voron machines already have such a design with their rear exhaust housing for HEPA filters.

The negative pressure will also eliminate diffusion, especially if your build chamber is not completely sealed.

---
### Back: [Voron V2.4R2 kit by Lecktor](../Readme.md)

# Sources:
[Nevermore Github](https://github.com/nevermore3d/Nevermore_Micro)

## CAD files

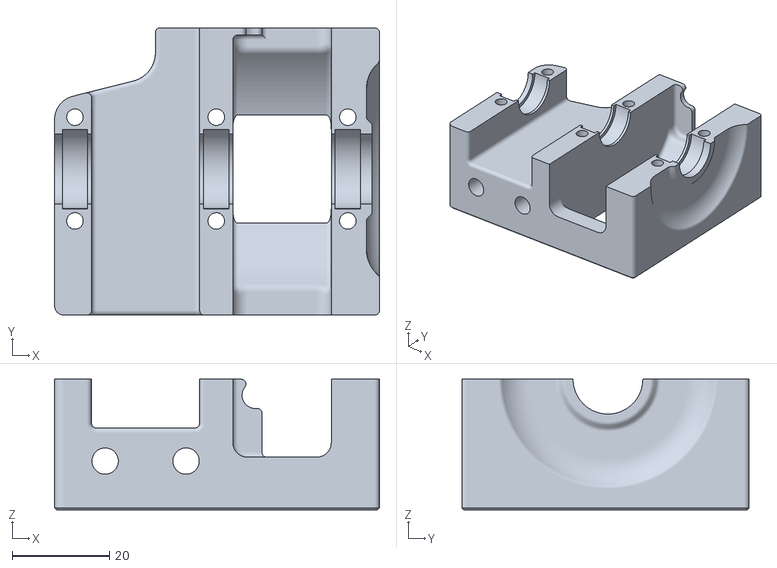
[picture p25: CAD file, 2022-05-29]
STL/Z_Drive/z_drive_main_a_x2.stl
66.7 x 59.0 x 26.8

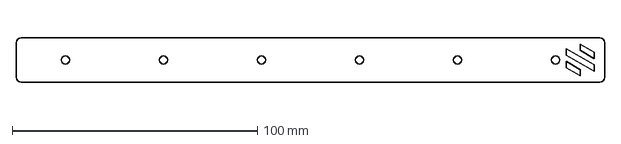
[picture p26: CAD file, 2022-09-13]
Backers/DXFs/Y_backer-200.dxf
240.0 x 18.0 mm

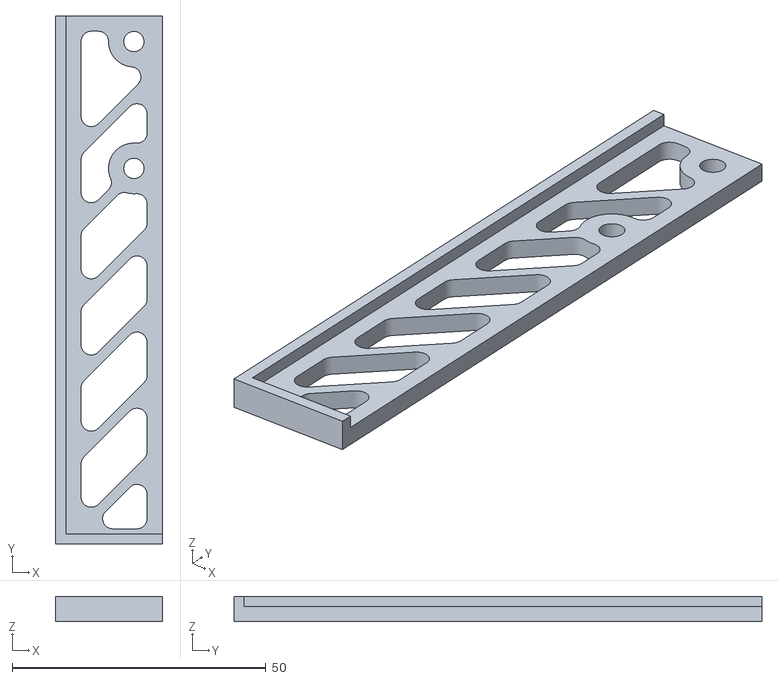
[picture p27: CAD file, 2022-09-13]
Door_Hinges/drill_guide_hinge.stl
21.0 x 104.0 x 5.00

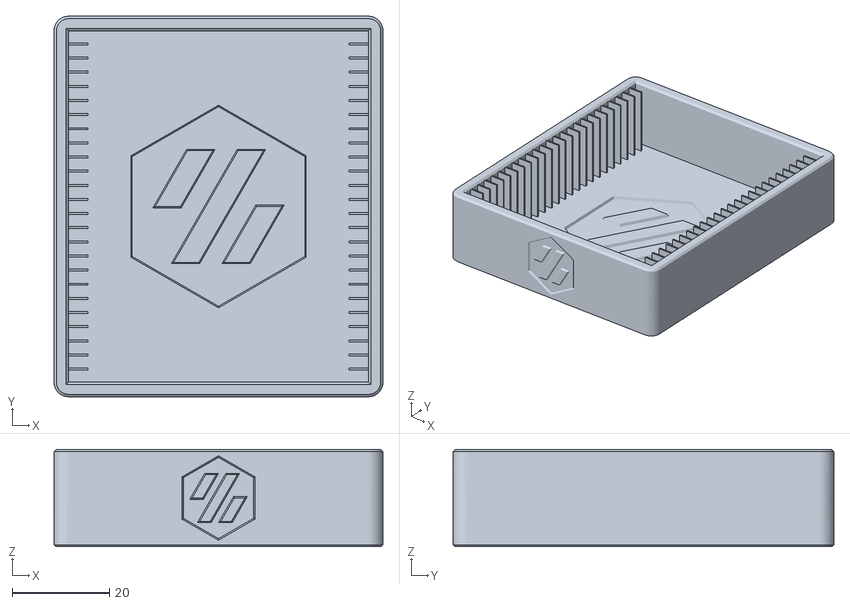
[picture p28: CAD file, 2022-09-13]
Manuals/Test_Prints/Filament_Card/Filament_Card_Caddy_25.stl
67.5 x 78.1 x 20.0

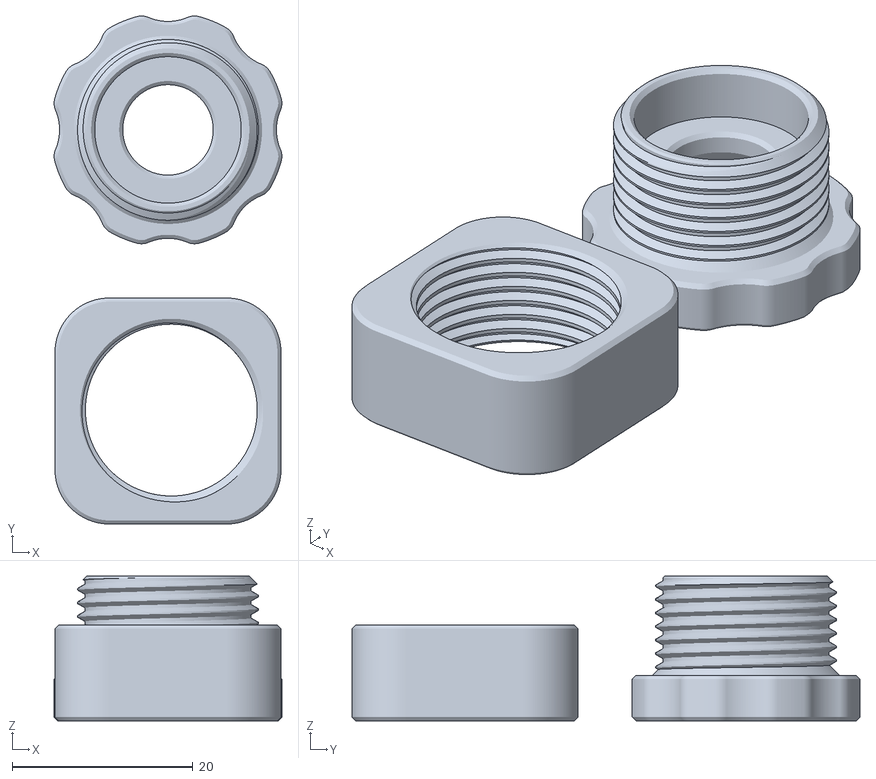
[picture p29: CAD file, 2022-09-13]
Manuals/Test_Prints/Thread_Tests/Thread_Test_1_x1_Rev1.STL
25.2 x 56.2 x 16.0

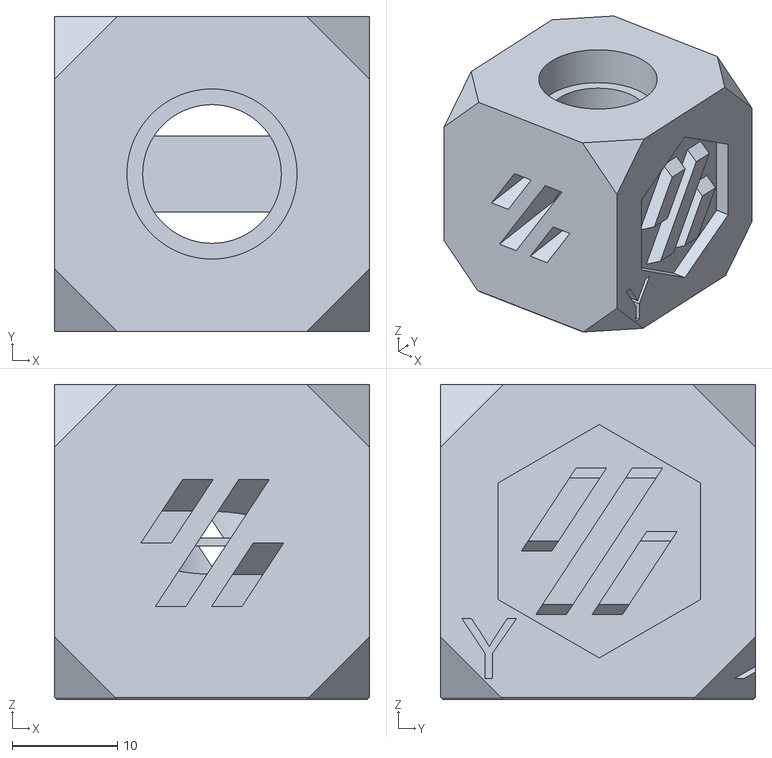
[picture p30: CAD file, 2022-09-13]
Manuals/Test_Prints/Voron_Design_Cube_v7.stl
30.0 x 30.0 x 30.0

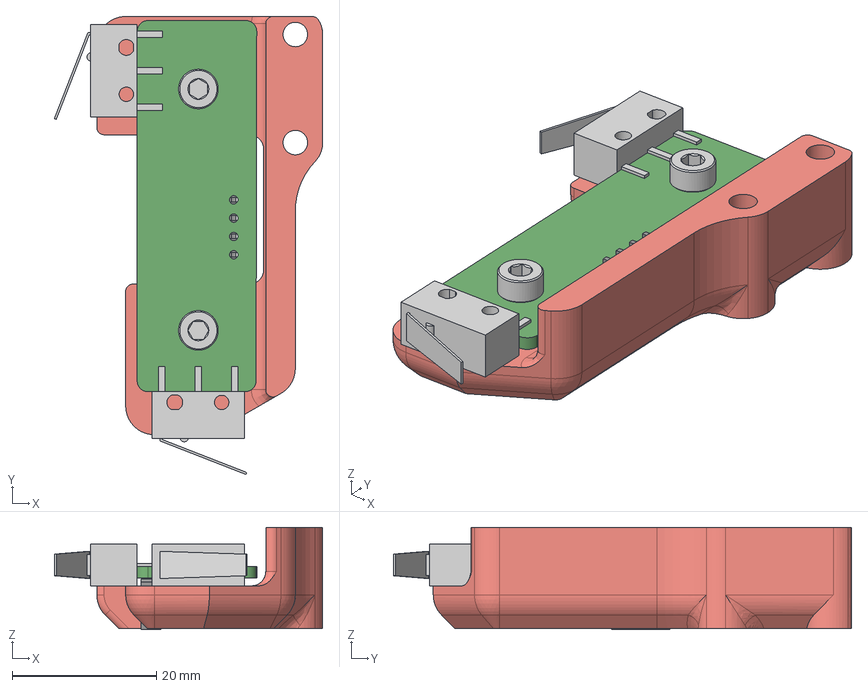
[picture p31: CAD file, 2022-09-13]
Microswitch_Endstop/Microswitch_Edge_Pod.step
37.3 x 63.6 x 14.2 mm
M3x8 SHCS (1) (1) (1) x 2

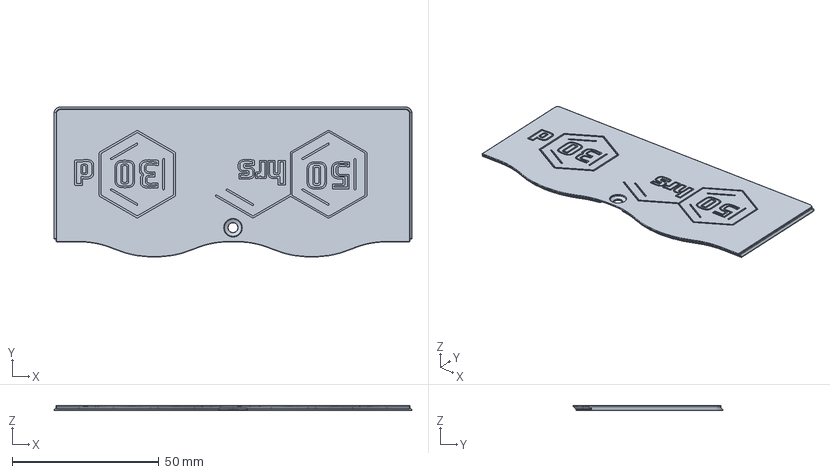
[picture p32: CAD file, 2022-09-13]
NeverMore/V5_Duo/DuoCartridgeLid.step
122.0 x 51.2 x 1.78 mm

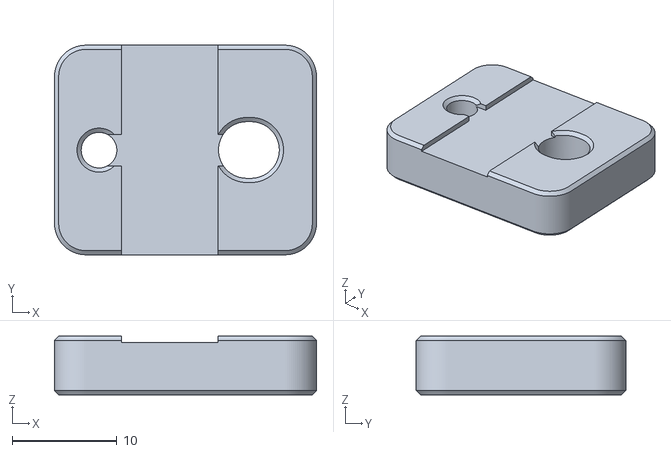
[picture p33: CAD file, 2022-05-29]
STL/Gantry/[a]_z_belt_clip_lower_x4.stl
25.0 x 20.0 x 5.60

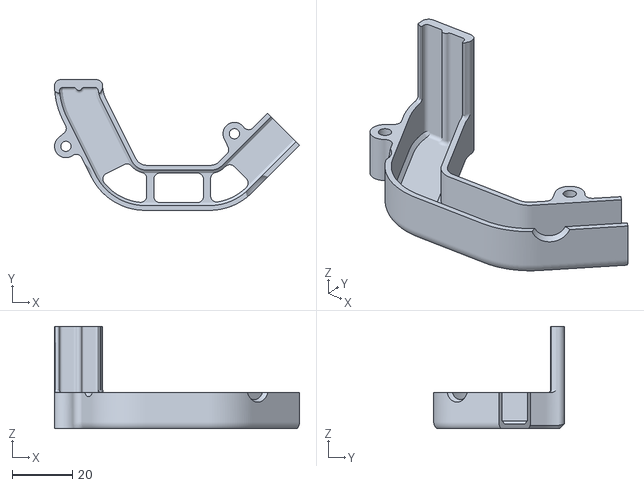
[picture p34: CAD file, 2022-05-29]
STL/Gantry/AB_Drive_Units/[a]_cable_cover.stl
81.5 x 43.5 x 34.0

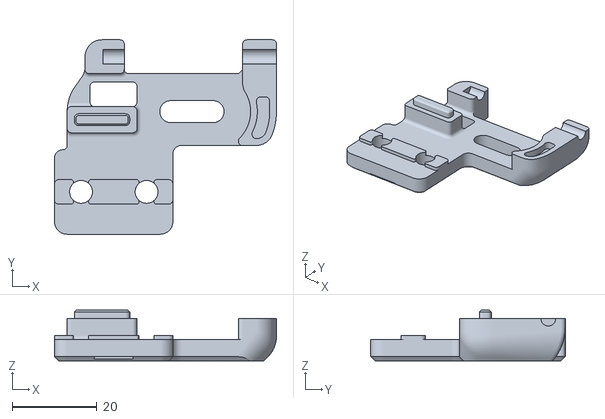
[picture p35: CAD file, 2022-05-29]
STL/Gantry/Front_Idlers/front_idler_right_upper (7).stl
52.5 x 46.0 x 12.0

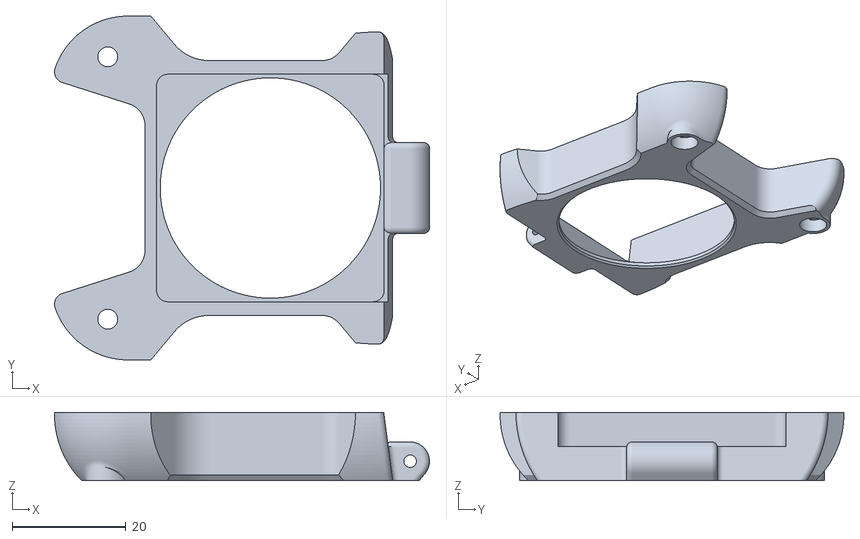
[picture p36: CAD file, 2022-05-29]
STL/Gantry/X_Axis/AfterBurner/hotend_fan_mount.stl
66.1 x 60.6 x 12.0

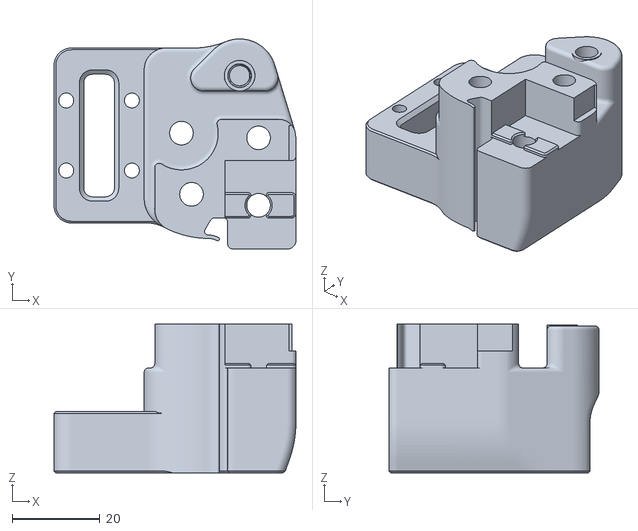
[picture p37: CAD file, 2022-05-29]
STL/Gantry/X_Axis/XY_Joints/xy_joint_right_lower_MGN12.stl
55.3 x 48.0 x 34.0

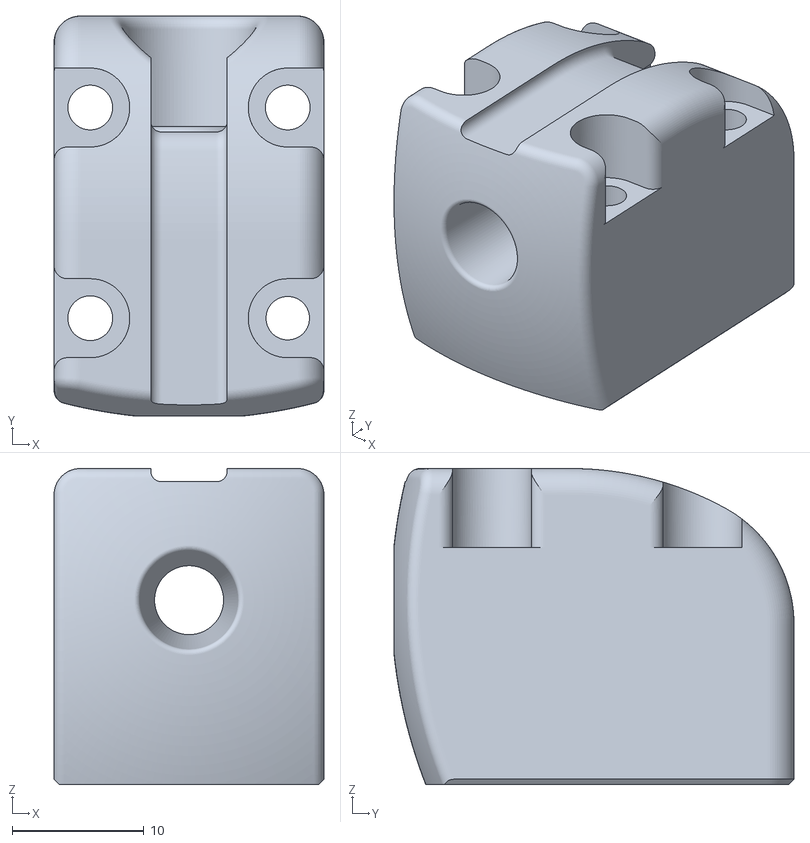
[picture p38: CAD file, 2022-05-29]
STL/Gantry/Z_Joints/z_joint_lower_x4.stl
20.5 x 30.4 x 24.0

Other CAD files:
STL/Z_Drive/z_drive_main_b_x2.stl
NeverMore/V5_Duo/V2/Duo_Cartridge_LID.stl
STL/Panel_Mounting/back_panel/bp_corner_clip_5mm_x4.stl
STL/Panel_Mounting/bottom_panel/bottom_panel_hinge_x2.stl
Backers/CAD/backer_sim.f3z
Backers/DXFs/X_backer_chain-200.dxf
Backers/DXFs/X_backer_chain-250.dxf
Backers/DXFs/X_backer_chain-300.dxf
Backers/DXFs/X_backer_chain-350.dxf
Backers/DXFs/Y_backer-250.dxf
Backers/DXFs/Y_backer-300.dxf
Backers/DXFs/Y_backer-350.dxf
Backers/DXFs/Y_backer_chain-200.dxf
Backers/DXFs/Y_backer_chain-250.dxf
Backers/DXFs/Y_backer_chain-300.dxf
Backers/DXFs/Y_backer_chain-350.dxf
BuildPlates/Universal/Voron_Universal_250x250_BuildPlate.f3d
BuildPlates/Universal/Voron_Universal_300x300_BuildPlate.f3d
BuildPlates/Universal/Voron_Universal_350x350_BuildPlate.f3d
BuildPlates/Voron_V2.4_250x250_BuildPlate.f3d
BuildPlates/Voron_V2.4_300x300_BuildPlate.f3d
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

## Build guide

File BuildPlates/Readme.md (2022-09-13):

# Voron V2.4R2 Build Plates (250, 300, 350)

---
### Back: [Voron V2.4R2 kit by Lecktor](../Readme.md)

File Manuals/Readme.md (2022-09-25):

# Manual for V2.4R2 kit by Lecktor

First up, assembly. We have produced modified Manual that should make assembly easy. Please read the manual through the first time before starting your assembly as it will make understanding the relations between objects much more easier. All heat inserts are done so those steps are for you to just verify that all of them are inserted. Should there be any missing, you have tooltip and inserts to add finishing touches.

* [Assembly Manual Voron V2.4R2 Lecktor Kit](AssemblyManual.pdf)

## Choosing Fluidd vs Mainsail
You should keep always your devices behind VPN for additional security. That being said, Fluidd supports user accounts while MainsailOS is wide open in your home network. Both are amazing lightweight tools to handle your Voron and since they are simple frontends for configuration, you can easily swap between them.

## Dive into manuals
* [MainsailOS Installation](./OperatingSoftware/MainsailOs.md) / [Fuidd Installation](./OperatingSoftware/Fluidd.md)
  * [Slicer Configuration Files](./Slicer)
* [Fysetc Spider V2.2 Firmware Image, Flash](./MCU_Firmware/Readme.md)
* [Klipper Configuration](./Klipper)
* [Testing Configuration](./Testing/Readme.md)
* [Tuning the printer](./Tuning/Readme.md)

## Visual guidance
If you want to see how assembly of a Voron would look like, step-by-step, there is a great fella on YouTube named [Scott Corn](https://www.youtube.com/watch?v=aHWiCs52pK4&list=PLSdS8RXoNhoRzDMZr9bK9-mfZjJzyWP8E) who has made a series from assembly of Voron V2.4. Your kit is V2.4R2 with some extra goodies so gantry and toolhead will be different for you. 

---
### Back: [Voron V2.4R2 kit by Lecktor](../Readme.md)

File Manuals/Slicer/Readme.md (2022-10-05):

# Notes about slicer

1. You need to adjust slicer profile per material you are using
2. If you are not using 350mm bed, adjust bed size.
3. If you are using different nozzle, then adjust it's size.
4. We recommend using [SuperSlicer](https://github.com/supermerill/SuperSlicer) for Voron Printers but you can also use [PrusaSlicer](https://github.com/prusa3d/PrusaSlicer).
5. Select Voron V2.4 Afterburner 0.4 nozzle as it closest default preset in slicer. This should be your starting point for trying to print.
6. You can import PIF profiles in this folder, but please do read first on 
[Ellis-PIF-Profile](https://github.com/AndrewEllis93/Ellis-PIF-Profile). These files are for printer that has resolved it's teething issues.

## Voron 2.4 Bed STL for PrusaSlicer and SuperSlicer
Download the appropriate STL for your bed size

Import under Printer Settings > General > Bed Shape (Set ...) > Model (Load...)

## Where to set the model and textures:
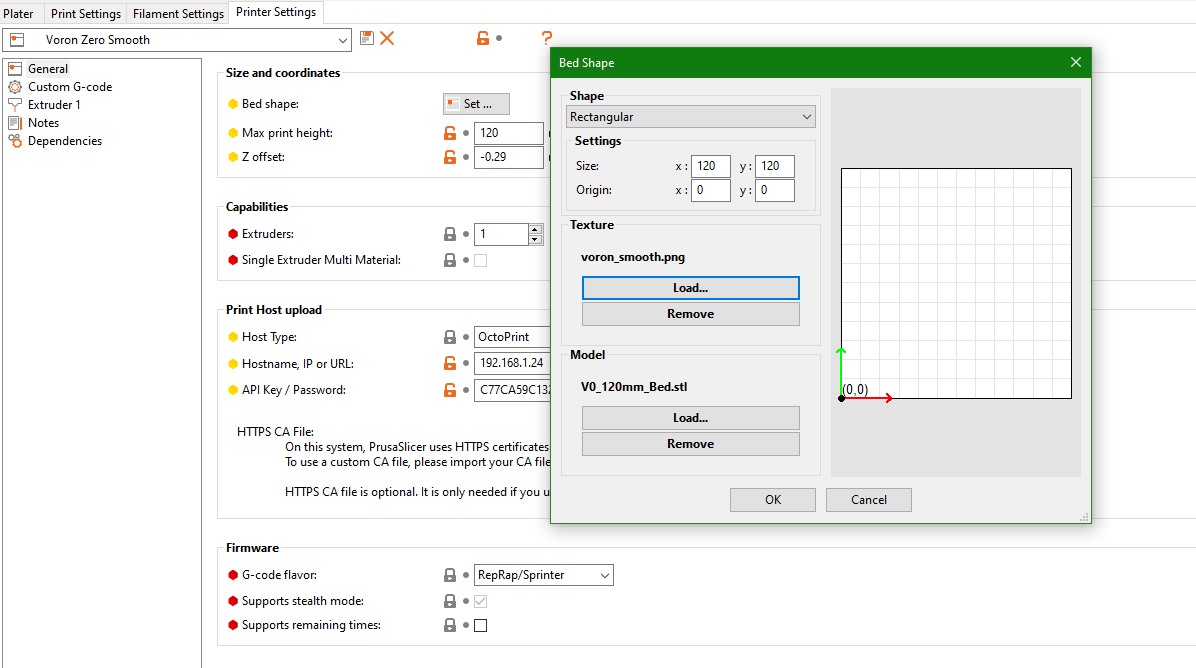
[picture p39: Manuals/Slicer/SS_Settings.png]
Examples
 

---
### Back: [Manuals](../Readme.md)

# Sources:
[Voron Extras Github](https://github.com/VoronDesign/Voron-Extras)  
[Voron 2 Github](https://github.com/VoronDesign/Voron-2)
[Voron Design Docs - Slicer](https://docs.vorondesign.com/build/slicer/)  
[Ellis-PIF-Profile](https://github.com/AndrewEllis93/Ellis-PIF-Profile)

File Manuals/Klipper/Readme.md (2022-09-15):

# Software configuration and testing

## First things first
1. You need to adjust Spider serial (line 17 in printer.cfg) to match yours. 
2. The configuration is preset for 350mm, go trough the configuration and adjust it in positions where you see 250mm or 300mm variants if you have different size kit.
3. Before heating the bed for first time, make sure it is only tightened in one corner (preferably the one next to the z-endstop sensor). If you need to do any adjustments with wires afterwards but before you have finished with bed make sure to temporarily tighten the bed down for that procedure.
4. Depending on you going with Fluidd or Mainsail way, only upload configs from respectable folders.

### Next: [Testing your work](../Testing/Readme.md)

---
### Back: [Manuals](../Readme.md)

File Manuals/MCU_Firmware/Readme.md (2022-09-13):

# SPIDER V2.2 MCU FW INSTALL/UPDATE

The firmware installation process for the Fysetc Spider MCU

## Prerequisites:

- Klipper must be installed onto the Raspberry Pi
- Take two blue jumpers out of the Fysetc Spider box
- You should have physical access to the MCU
- Voron Design recommends using USB to control the Spider, which simply requires connecting a USB-A to USB-C cable between the Spider and Pi. If you prefer a UART connection, please consult the fysetc documentation for the necessary configuration adjustments.
- For DFU mode and flashing, please remove the display cables from Spider board. You should mark the cables with 1 and 2 to help with reconnection at later stage.

# 1. Enter DFU Mode

1.  First power off the board

2. Set jumper on 5v pin and DC5V 
5V Jumper
3. Place jumper on BT0 to 3.3V pin 
DFU Jumper
4. Connect USB cable to the board and RPI

5. Power up the board with 24v

# 2. Build Firmware Image

- Login to the Raspberry Pi via ssh
    ```
    username: pi
    pass: raspberry
    ```
- Run the following:
    ```
    sudo apt install make
    cd ~/klipper
    make clean
    make menuconfig
    ```
- In the menu structure there are a number of items to be selected.
    - Select “Enable extra low-level configuration options”
    - Set the micro-controller architecture is set to STMicroelectronics STM32
    - Set the Processor model to STM32F446
    - Set the Bootloader offset to 32KiB bootloader
    - If your Spider was made prior to 2021/06/23, set the Bootloader offset to 64KiB bootloader
    - Set the Clock Reference to 12 MHz crystal
    - Set the Communication interface to USB (on PA11/PA12) (note: see Fysetc documentation if you intend to use UART rather than USB)
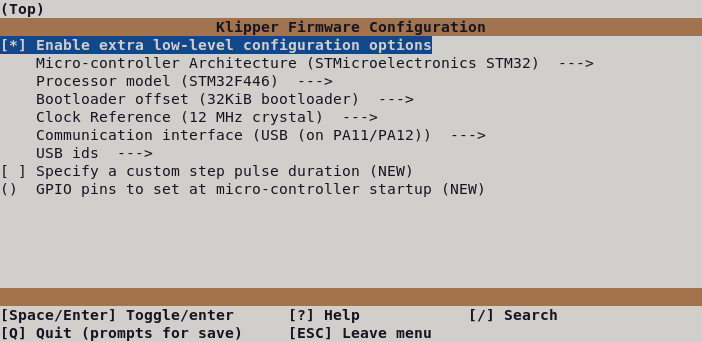
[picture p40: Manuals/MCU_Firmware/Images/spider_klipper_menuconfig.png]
Spider Klipper Menu Config


- Once the configuration is selected, press ```q``` to exit, and ```“Yes”``` when asked to save the configuration.

- Run the command
    ```
    make
    ```

- The make command, when completed, creates a firmware file klipper.bin which is stored in the folder /home/pi/klipper/out.

# 3. Firmware Installation

- From your ssh session, run 
    ```
    lsusb
    ```
    and find the ID of the DFU device.
- Run command below replacing 1234:5678 with the ID from the previous step 
    ```
    make flash FLASH_DEVICE=1234:5678
    ```

# 4. Exit DFU Mode

- Power off the Spider
- Remove the jumper from BT0/3.3V
- Power up the Spider
- You can confirm that the flash was successful by running
    ```
    ls /dev/serial/by-id
    ```
If the flash was successful, this should now show a klipper device, similar to:
Serial of Device

You will need to write that serial down and use it in printer.cfg as this is your device specific ID! You should power down the printer and connect display cables to Spyder now.

### Next: [Klipper configuration](../Klipper/Readme.md)

---
### Back: [Manuals](../Readme.md)

# Sources:
[Voron Design Wiki](https://docs.vorondesign.com/build/software/spider_klipper.html)  
[Fysetc Spider Wiki](https://wiki.fysetc.com/Spider/)

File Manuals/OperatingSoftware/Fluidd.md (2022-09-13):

# Installing Fluidd

The recommended way to install Fluidd on a Raspberry Pi is to use [FluiddPi](#FluiddPi), a pre-packaged disk image. 

## FluiddPi

To install Fluidd on a Raspberry Pi:
1. Download the latest fluiddPi  [Release](https://github.com/cadriel/FluiddPI/releases)
2. Unzip the .img file from your download.
3. Use [BalenaEtcher](https://www.balena.io/etcher/) to write the .img to an 8GB (or larger) microSD card.  *THIS WILL DESTROY ALL DATA ON YOUR CARD*. 
4. If you will be using wifi, edit the file `fluiddpi-wpa-supplicant.txt` with your Wifi information. If you are having trouble seeing this file on the microSD card, try removing it and re-inserting it into your card reader.
5. Make sure that your MCU(s) is connected to your pi. If you will be using wired networking, also make sure your ethernet cable is connected.
6. Insert the microSD card into your Pi, and power on the Pi.    
7. Find your Pi on the network, and ssh into it (using PuTTY on Windows or the terminal on MacOS)
  
   The default username is `pi` and the password is `raspberry`.
    * If your network supports bonjour, the pi should show up as `fluiddpi.local`
    * If your network automatically assigns DNS hostnames, it may simply show up as `fluiddpi`
    * Failing these two options, you may need to check your router's DHCP server, and find out what IP address as been assigned to the device.
8. Connect to your Pi in a web browser: [http://fluiddpi.local](http://fluiddpi.local) (or whatever you determined the hostname/IP to be in the previous step)
9.   When you first connect, fluiddpi will ask you to "provide the moonraker API URL":  enter the same host name or IP address once more.  (`fluiddpi.local`)

### Software Update
 
As soon as you have Fluiddpi loaded, it is highly recommended that you make sure all the software is up to date.  (At times, the downloaded image file contains fairly out of date software.)

1. Access Fluidd through a web browser, using whatever IP or hostname you found above.  
(Note, you will see some errors regarding the non-configured state of your printer.  These can be ignored… for now)
2. Click the "Settings" button on the left side of the screen
3. Scroll down to the  "Software Updates" section
4. Click the "check for updates" button
5. Click "update" for each component that needs it.

### Next: [Firmware Flashing](../MCU_Firmware/Readme.md)

---
### Back: [Manuals](../Readme.md)

# Sources:
[Voron Design Wiki Fluidd](https://docs.vorondesign.com/build/software/installing_fluidd.html)  
[Fluidd](https://docs.fluidd.xyz/)

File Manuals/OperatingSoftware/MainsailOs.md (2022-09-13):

# Installing Mainsail

The recommended way to install Mainsail on a Raspberry Pi is to use [MainsailOS](https://docs.mainsail.xyz/), a pre-packaged disk image. If you are building a custom configuration, you may need to skip these instructions and install Mainsail [manually](#mainsail-manual-installation).

## MainsailOS
To install Mainsail on a Raspberry Pi:
1. Download and install [pi-imager](https://www.raspberrypi.com/software/)
2. Click "Choose OS" and scroll down to "Other specific-purpose OS".
3. Select "3D Printing" and choose "Mainsail OS". 
4. Choose your SD Card. 
5. If you will be using wifi, click on the GEAR icon in the bottom right corner and enter your wifi information. DO NOT EDIT THE USERNAME. 
6. Click on "SAVE" and on "WRITE". *THIS WILL DESTROY ALL DATA ON YOUR CARD*.
7. Make sure that your MCU(s) is connected to your pi. If you will be using wired networking, also make sure your ethernet cable is connected.
8. Insert the microSD card into your Pi, and power on the Pi.    
9. Find your Pi on the network, and ssh into it (using PuTTY on Windows or the terminal on MacOS)  
   
   The default username is `pi` and the password is `raspberry`.
    * If your network supports bonjour, the pi should show up as `mainsailos.local`
    * If your network automatically assigns DNS hostnames, it may simply show up as `mainsailos`
    * Failing these two options, you may need to check your router's DHCP server, and find out what IP address as been assigned to the device.
 
### Software Update
As soon as you have MainsailOS loaded, it is highly recommended that you make sure all the software is up to date.  (At times, the downloaded image file contains fairly out of date software.)

1. Access Mainsail through a web browser, using whatever IP or hostname you found above.  
(Note, you will see some errors regarding the non-configured state of your printer.  These can be ignored… for now)
2. Click the "Machine" button on the left side of the screen
3. In the "Update Manager" panel, click the refresh button
4. Click the "Update" button for each component that needs updating.

### Next: [Firmware Flashing](../MCU_Firmware/Readme.md)

## Mainsail Manual Installation
The Mainsail manual installation process is documented in [the Mainsail docs](https://docs.mainsail.xyz/setup/manual-setup).

---
### Back: [Manuals](../Readme.md)

# Sources:
[Voron Design Wiki Mainsail](https://docs.vorondesign.com/build/software/installing_mainsail.html#MainsailOS)  
[Mainsail](https://docs.mainsail.xyz/)

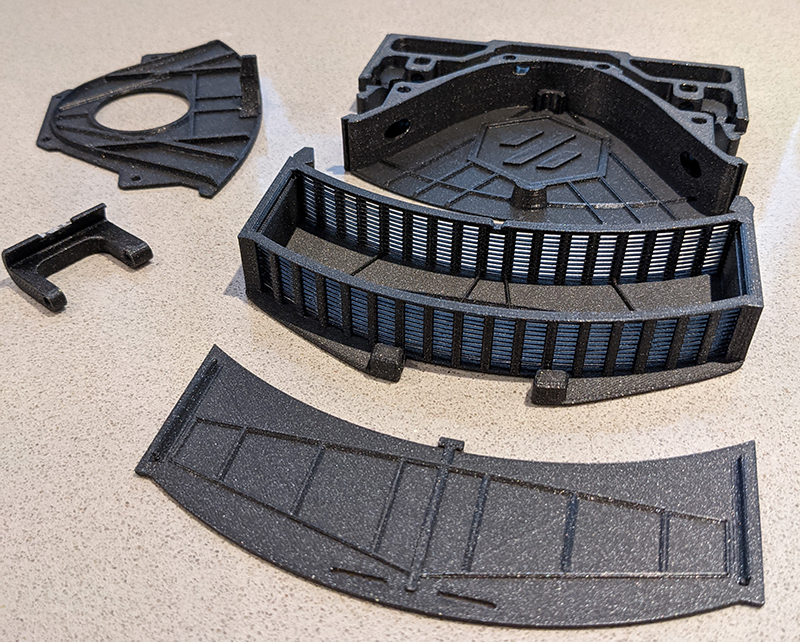
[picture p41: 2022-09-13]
NeverMore/images/print_example2.png

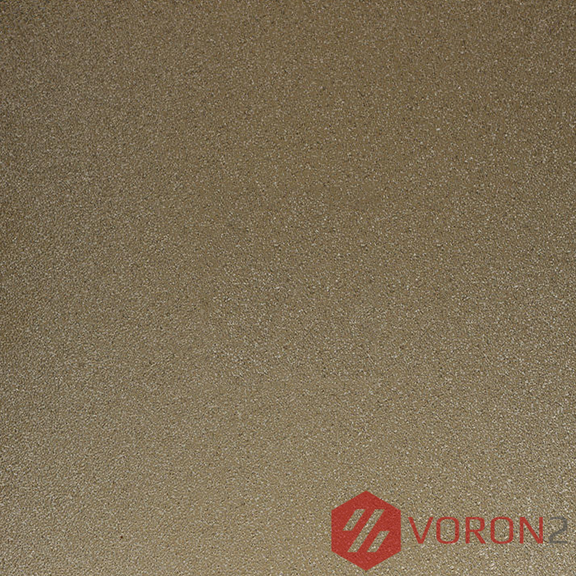
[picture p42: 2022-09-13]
Manuals/Slicer/Bed Models/V2_bed_textured_pei.png

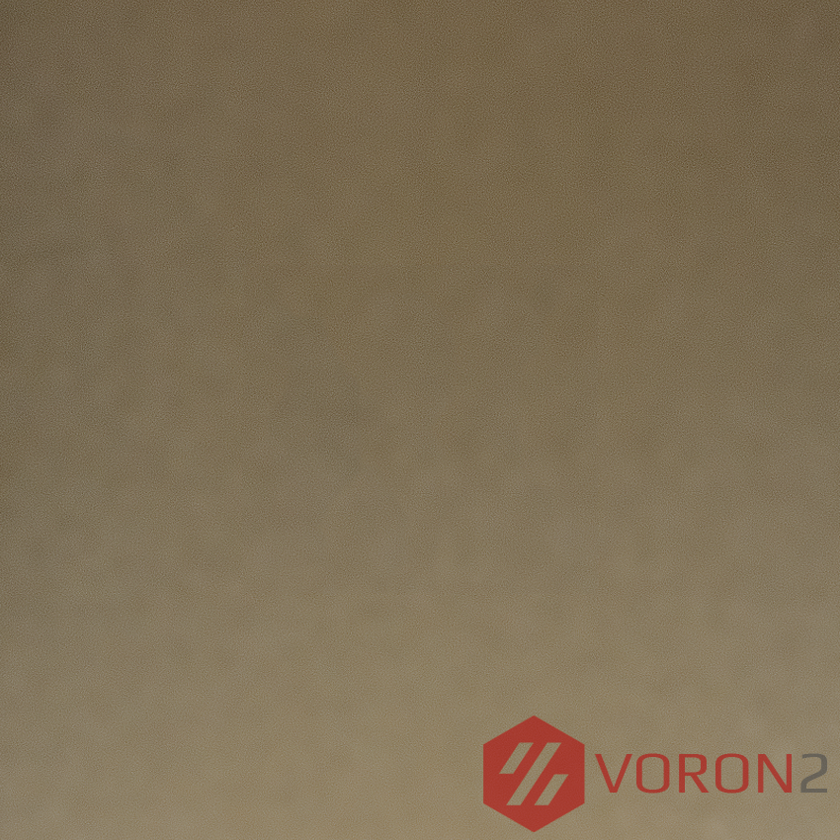
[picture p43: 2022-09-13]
Manuals/Slicer/Bed Models/V2_bed_smooth_pei.png

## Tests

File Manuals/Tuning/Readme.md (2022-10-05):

# Tuning the printer
1. **PID_CALIBRATE HEATER=heater_bed TARGET=100**
   1. This will take ~10min
   2. Once this is done, use **SAVE_CONFIG**
2. Run **M106 S64** command <- this will turn on the part cooling fan at 25%
3. Run **PID_CALIBRATE HEATER=extruder TARGET=245** command
   1. Once this is done, use **SAVE_CONFIG**
4. When cabin is hot, tighten ***all*** the screws. If you tighten the screws later, you need to do calibration again.
5. Next up take a ruler and try to get gantry as even as possible on both sides.
   1. Make sure the nozzle will clear the bed
   2. Run **G28** command
   3. Press QGL to start automatic leveling
      1. The probe will measure distance in all four corners and adjust is each corner automatically until all corners are adjusted. It will try up to five times before giving up.
      2. Tolerance allowed is ***0.00750***, if you did your assembly correctly, it should be no problem to beat.
6. Extruder
   1. Add bowden to the the toolhead
   2. Try to extrude filament, configuration is already tuned for you
7. Z-Endstop calibration
   1. Once the chamber has heated up (set extruder to 240, heat bed to 100)
   2. Add a sheet of paper between the bed and toolhead
   3. Run **Z_ENDSTOP_CALIBRATE** command
      1. Then run **TESTZ Z=-1** command until the nozzle is close to the paper
      2. If you go too far, run **TESTZ Z=1** command
      3. Once you are close, switch to **TESTZ Z=-0.1** command
      4. Do this until you feel a drag on the paper when moving it
      5. Remove the paper
      6. Beacuse we did this hot, we need to run one more **TESTZ Z=-0.1** command
      7. Run **ACCEPT** command
      8. Run **SAVE_CONFIG** command
      9. The nozzle bed offset is done for now.
8.  Bed heightmap calibration
    1.  Select from menu heightmap
    2.  Press on calibrate button
        1.  A good result of your work should be having variance of less than 0.3mm. 
            1.  Things that can affect this: uneven bed magnet application, uneven surfaces of bed sheet, bed itself, uneven gantry or frame, to fast bed heating. The reason why we do this heightmap is to cancel out any imperfections via software. 
    3.  Save with provided name "default" <- this way, it will be automatically picked up by config you imported earlier.
    4.  Run **SAVE_CONFIG** command

Thats it for tuning. You should be now ready for your first print. If you had any issues along the way, you can take a look at [very detailed tuning guide](https://github.com/AndrewEllis93/Print-Tuning-Guide) by AndrewEllis93. You can also find some helpful tuning print files [here](../Test_Prints/).

> **PS:** For configuring MainsailOS from SSH, enter **SUDO raspi-config**. From there you can join your device to WiFi should you choose to do so and change local network domain name.

Don't have an idea what to print? Try printing a [cube](https://www.thingiverse.com/thing:5429894) and filming it for [serial request](https://www.reddit.com/r/voroncorexy/). Please read about the process in [this serial request information questions reddit thread](https://www.reddit.com/r/voroncorexy/comments/r4ggml/serial_request_information_questions/).

---
### Back: [Manuals](../Readme.md)

# Sources:
[Youtube: Voron 2.4 Step By Step Part 13 Tuning, SuperSlicer and First Print](https://youtu.be/1wBi1mXVVEQ)  
[Voron Design Docs - Initial Startup](https://docs.vorondesign.com/build/startup/)  
[Voron Design Docs - First Print](https://docs.vorondesign.com/build/slicer/first_print.html)

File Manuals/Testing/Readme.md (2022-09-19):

# Testing your work
1. Go to your printer management gui on web.
2. Turn on heater for extruder and set it to ***50C***. Wait for it to reach temp. Once temp is reached and it's not climbing past it, turn it off and wait for temp to go down.
3. Turn on heater for bed and set it to ***50C***. Wait for it to reach temp. Once temp is reached and it's not climbing past it, turn it off and wait for temp to go down.
4. Next up we want to test motors, for that run command:
   1. **STEPPER_BUZZ STEPPER=stepper_x** <- this causes b motor to move
   2. **STEPPER_BUZZ STEPPER=stepper_y** <- this causes a motor to move
   3. **STEPPER_BUZZ STEPPER=stepper_z** <- this is the front left corner
   4. **STEPPER_BUZZ STEPPER=stepper_z1** <- the back left corner
   5. **STEPPER_BUZZ STEPPER=stepper_z2** <- the back right corner
   6. **STEPPER_BUZZ STEPPER=stepper_z3** <- the front right corner
   7. **STEPPER_BUZZ STEPPER=extruder** <- the print head gears
5. Next up testing the end stops. Put print head in the centre of the printer.
   1. Go to Machine, refresh endstop statuses
   2. Hold down the X endstop switch, press refresh on endstop statuses
      1. It should state that it's now triggered instead of being open.
      2. Repeat steps for Y and Z endstop.
   3. Take a metal object (e.g. Caliper) and place it under the Omron proximity sensor. Press refresh on endstop statuses, it should state that it's now triggered instead of being open.
6. Testing Homing
   1. Go to console and run **G28 x** command <- the printhead will go up a little and then to the right until it hits the X endstop.
   2. Next run **G28 y** command <- the printhead will go up a little and then back until it hits the Y endstop
   3. Shut down your printer. Without moving the print head lower the gantry to bed level.
      1. Measure from the back of the bed to the centre of the print nozzel
      2. The centre of the Z endstop pin needs to be that far back from the bed.
         1. You can now fully tighten down the Z endstop.
      3. The bed needs to be moved back, so that it is ***2-3mm*** from the closest edge of the Z endstop pin.
         1. Loosen bed screws for easy moving. Tighten ***only*** screw near the Z-endstop after that.
      4. Align the print nozzle with the Z endstop on the X axis, then move the print head to the center on the Y axis.
   4. Power up your printer and send a **G28 y** command
      1. Without changing X or Y lower the gantry, until the nozzle touches the Z endstop, the nozzle should be in the centre of the pin
         1. Z endstop should be higher than the bed
   5. Testing the 0,0 location
      1. Move the print head close but not touching to the bed, in centre.
      2. Run **G28 x y** command to put the print head in the back right corner.
      3. Using Controls from UI, move the print head close to the front left corner
      4. Once you are close, run **M114**, it will show your position
      5. Move the ammounts needed to be at 0,0
         1. You should be on the corner of the bed. It is probably a good idea it rather be in a small amount, you can change it in tuning should you feel the need for it.
   6. Finding the X, Y of the Z endstop
      1. Start with **G28 x y** command
      2. Using Controls from UI , move the print head over until it lines up with the Z endstop.
      3. Run **M114** command so we get X and Y coordinates
      4. Save the result of those coordinates to Notepad
      5. Open up printer.cfg, search for safe_z_home, on line 393 you should see coordinates. Adjust them to the previous step results.
      6. Save and apply configuration
      7. After new conf is loaded, run **G28 x y z**
   7. Testing probe accuracy
      1. Run **PROBE_ACCURACY** command <- The probe will go close down to bed 10 times. From results you are looking for standard deviation of less than 0.003mm.

### Next: [Tuning the printer](../Tuning/Readme.md)

---
### Back: [Manuals](../Readme.md)

# Sources:
[YouTube: Voron 2.4 Step By Step Part 12 Software, Configuration and Testing](https://youtu.be/yfRtpPPcnN8)  
[Voron Design Docs - Initial Startup](https://docs.vorondesign.com/build/startup/)

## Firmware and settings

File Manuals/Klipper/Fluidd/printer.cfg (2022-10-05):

## Voron Design VORON 2.4R2 250/300/350mm with Spider config, Lecktor kit

## *** THINGS TO CHANGE/CHECK: ***
## MCU paths							        [mcu] section
## Thermistor types						        [extruder] and [heater_bed] sections - See 'sensor types' list at end of file
## Z Endstop Switch location	                [safe_z_home] section
## Homing end position				            [gcode_macro G32] section
## Z Endstop Switch  offset for Z0	            [stepper_z] section
## Probe points							        [quad_gantry_level] section
## Min & Max gantry corner postions	            [quad_gantry_level] section
## PID tune								        [extruder] and [heater_bed] sections
## Fine tune E steps					        [extruder] section

## *** FOR REFERENCE ***
##
## ^PA1 - X endstop
## ^PA2 - Y endstop
## ^PA3 - proximity probe
## ^PB14 - unused 
## PB13 - Case Leds
## ^PA0 - Z-endstop
## PB0 - Bed thermistor
## PC0 - Hot-End thermistor
## PA13 - EFAN
## PA14 - PFAN
## PB2 - Nevermore fans
##

[mcu]
##	Obtain definition by "ls -l /dev/serial/by-id/" 
##--------------------------------------------------------------------
serial: /dev/serial/by-id/usb-Klipper_stm32f446xx_2B002A001151383039343538-if00

## Uncomment below if you're using the Raspberry uart0 to communicate with Spider
#restart_method: command

[printer]
kinematics: corexy
max_velocity: 300  
max_accel: 3000			        #Max 4000
max_z_velocity: 15			    #Max 15 for 12V TMC Drivers, can increase for 24V
max_z_accel: 350
square_corner_velocity: 5.0

#####################################################################
#      X/Y Stepper Settings
#####################################################################

[stepper_x]
##	Connected to X-MOT (B Motor)
step_pin: PE11
dir_pin: PE10
enable_pin: !PE9
rotation_distance: 40
microsteps: 32
full_steps_per_rotation:400  #set to 400 for 0.9 degree stepper
endstop_pin: ^PA1 
position_min: 0

##--------------------------------------------------------------------

##	Uncomment below for 250mm build
#position_endstop: 250
#position_max: 250

##	Uncomment for 300mm build
#position_endstop: 300
#position_max: 300

#	Uncomment for 350mm build
position_endstop: 350
position_max: 350

##--------------------------------------------------------------------
homing_speed: 100   #Max 100
homing_retract_dist: 5
homing_positive_dir: true

##	Make sure to update below for your relevant driver (2208 or 2209)
[tmc2209 stepper_x]
uart_pin: PE7
interpolate: False
run_current: 0.8
sense_resistor: 0.110
stealthchop_threshold: 0

[stepper_y]
##	Connected to Y-MOT (A Motor)
step_pin: PD8
dir_pin: PB12
enable_pin: !PD9
rotation_distance: 40
microsteps: 32
full_steps_per_rotation:400  #set to 400 for 0.9 degree stepper
endstop_pin: ^PA2
position_min: -10
##--------------------------------------------------------------------

##	Uncomment for 250mm build
#position_endstop: 250
#position_max: 250

##	Uncomment for 300mm build
#position_endstop: 300
#position_max: 300

#	Uncomment for 350mm build
position_endstop: 355
position_max: 355

##--------------------------------------------------------------------
homing_speed: 100  #Max 100
homing_retract_dist: 5
homing_positive_dir: true

##	Make sure to update below for your relevant driver (2208 or 2209)
[tmc2209 stepper_y]
uart_pin: PE15
interpolate: False
run_current: 0.8
sense_resistor: 0.110
stealthchop_threshold: 0

#####################################################################
#   Z Stepper Settings
#####################################################################

## In Z-MOT Position
## Z0 Stepper - Front Left
[stepper_z]
step_pin: PD14
dir_pin: !PD13
enable_pin: !PD15
rotation_distance: 40
gear_ratio: 80:16
microsteps: 32
##  In Z- Position
endstop_pin: ^PA0
##  Z-position of nozzle (in mm) to z-endstop trigger point relative to print surface (Z0)
##  (+) value = endstop above Z0, (-) value = endstop below
##	Increasing position_endstop brings nozzle closer to the bed
##  After you run Z_ENDSTOP_CALIBRATE, position_endstop will be stored at the very end of your config
position_endstop: 0
##--------------------------------------------------------------------

##	Uncomment below for 250mm build
#position_max: 230

##	Uncomment below for 300mm build
#position_max: 280

#	Uncomment below for 350mm build
position_max: 295

##--------------------------------------------------------------------
position_min: -5
homing_speed: 8
second_homing_speed: 3
homing_retract_dist: 3

##	Make sure to update below for your relevant driver (2208 or 2209)
[tmc2209 stepper_z]
uart_pin: PD10
interpolate: False
run_current: 0.8
sense_resistor: 0.110
stealthchop_threshold: 0

##	In E1-MOT Position
##	Z1 Stepper - Rear Left
[stepper_z1]
step_pin: PE6
dir_pin: PC13
enable_pin: !PE5
rotation_distance: 40
gear_ratio: 80:16
microsteps: 32

##	Make sure to update below for your relevant driver (2208 or 2209)
[tmc2209 stepper_z1]
uart_pin: PC14
interpolate: False
run_current: 0.8
sense_resistor: 0.110
stealthchop_threshold: 0

##	In E2-MOT Position
##	Z2 Stepper - Rear Right
[stepper_z2]
step_pin: PE2
dir_pin: !PE4
enable_pin: !PE3
rotation_distance: 40
gear_ratio: 80:16
microsteps: 32

##	Make sure to update below for your relevant driver (2208 or 2209)
[tmc2209 stepper_z2]
uart_pin: PC15
interpolate: False
run_current: 0.8
sense_resistor: 0.110
stealthchop_threshold: 0

##	In E3-MOT Position
##	Z3 Stepper - Front Right
[stepper_z3]
step_pin: PD12
dir_pin: PC4
enable_pin: !PE8
rotation_distance: 40
gear_ratio: 80:16
microsteps: 32

[tmc2209 stepper_z3]
uart_pin: PA15
interpolate: False
run_current: 0.8
sense_resistor: 0.110
stealthchop_threshold: 0

#######################################
#### Enclosure Temp Sensor Section ####
#######################################
##[thermistor chamber_temp]
##temperature1: 25
##resistance1: 10000
##beta: 3950


##[temperature_sensor enclosure_temp]
##sensor_type: chamber_temp
##sensor_pin: PC1
##min_temp: 0
##max_temp: 100
##gcode_id: C

#####################################################################
#   Extruder
#####################################################################

##	In E0-MOT Position
[extruder]
step_pin: PD5
dir_pin: !PD6
enable_pin: !PD4

##	Update value below when you perform extruder calibration
##	If you ask for 100mm of filament, but in reality it is 98mm:
##	rotation_distance = <previous_rotation_distance> * <actual_extrude_distance> / 100
##  22.6789511 is a good starting point for Bondtech 5mm gears
##  34.37086 for Bondtech 8mm gears (Galileo)
##  22.90574 # for Bondtech on afterburner
##  22.7923459 # for Bondtech on stealthburner
rotation_distance: 22.7923459 # CALIBRATED for Stealthburner
##	Update Gear Ratio depending on your Extruder Type
##	Use 50:17 for Afterburner/Clockwork (BMG Gear Ratio)
##	Use 80:20 for M4, M3.1
##  Use 7.5:1 for Galileo
gear_ratio: 5:1				#for Galileo
microsteps: 32
full_steps_per_rotation: 200	#200 for 1.8 degree, 400 for 0.9 degree
nozzle_diameter: 0.400
filament_diameter: 1.75
##      In E0 OUT Position
heater_pin: PB15
##	Validate the following thermistor type to make sure it is correct
sensor_type: ATC Semitec 104NT-4-R025H42G
sensor_pin: PC0
min_temp: 10
max_temp: 270
max_power: 1.0
min_extrude_temp: 180
control = pid
pid_kp = 26.213
pid_ki = 1.304
pid_kd = 131.721
#	Try to keep pressure_advance below 1.0
pressure_advance: 0.05
#	Default is 0.040, leave stock
pressure_advance_smooth_time: 0.040

##	In E0-MOT Position
##	Make sure to update below for your relevant driver (2208 or 2209)
[tmc2209 extruder]
uart_pin: PD7
interpolate: false
run_current: 0.5
hold_current: 0.2
sense_resistor: 0.110
stealthchop_threshold: 0

##[filament_switch_sensor RunoutSensor]
##pause_on_runout: False
##runout_gcode:  F_CONSUMED
##switch_pin: ^PB13
##event_delay: 4.0##

##[gcode_macro F_CONSUMED]
##variable_filament_consumed: 0
##variable_filament_lenght: 20   # length between the sensor and extruder
##gcode:
##    # save current filament consumption
##    SET_GCODE_VARIABLE MACRO=F_CONSUMED VARIABLE=filament_consumed VALUE={printer.print_stats.filament_used}
##    # start checking filament consumption
##    UPDATE_DELAYED_GCODE ID=DELAY_M600 DURATION=1##

##[delayed_gcode DELAY_M600]
##gcode:
##    # use set for easier reading
##    {% set consumed=printer["gcode_macro F_CONSUMED"].filament_consumed %}
##    {% set length=printer["gcode_macro F_CONSUMED"].filament_lenght %}
##    # check if predetermine length is reached
##    {% if printer.print_stats.filament_used|float <= (consumed|float + length|float) %}
##    # start looping this script every second
##    UPDATE_DELAYED_GCODE ID=DELAY_M600 DURATION=1
##    {% else %}
##    error_tones
##    PAUSE
##    {% endif %}
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

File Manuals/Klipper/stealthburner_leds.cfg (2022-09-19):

# Macros for setting the status leds on the Voron StealthBurner toolhead (or for any neopixel-type leds).
#
# You will need to configure a neopixel (or other addressable led, such as dotstar). See
# https://www.klipper3d.org/Config_Reference.html#neopixel for configuration details.


#####################################
#           INSTRUCTIONS            #
#####################################
# How to use all this stuff:
#
#     1.  Copy this .cfg file into your Klipper config directory and then add [include stealthburner_leds.cfg]
#         to the top of your printer.cfg in order for register the LEDs and macros with Klipper.
#     2.  Define your LEDs by editing [neopixel sb_leds] below and entering the data pin from your control board
#         as well as the color order.
#
#           Note: RGB and RGBW are different and must be defined explicitly.  RGB and RGBW are also not able to 
#                 be mix-and-matched in the same chain. A separate data line would be needed for proper functioning.
#
#                 RGBW LEDs will have a visible yellow-ish phosphor section to the chip.  If your LEDs do not have
#                 this yellow portion, you have RGB LEDs.
#
#     3.  Save your config and restart Klipper.
#
#           Note: We set RED and BLUE to 1.0 to make it easier for users and supporters to detect 
#                 misconfigurations or miswiring. The default color format is for Neopixels with a dedicated 
#                 white LED. On startup, all three SB LEDs should light up.
#
#                 If you get random colors across your LEDs, change the color_order to GRB and restart. Then
#                 omit the W for each suggested color_order in the next paragraph.
#
#                 If you get MAGENTA, your  color order is correct. If you get CYAN, you need to use RGBW. If
#                 you get YELLOW, you need to use BRGW (note that BRG is only supported in the latest Klipper
#                 version).
#
#     4.  Once you have confirmed that the LEDs are set up correctly, you must now decide where you want 
#         these macros called up...which means adding them to your existing gcode macros.  NOTHING will happen
#         unless you add the STATUS_????? macros to your existing gcode macros.  
#
#           Example: add STATUS_LEVELING to the beginning of your QGL gcode macro, and then add STATUS_READY 
#                    to the end of it to set the logo LED and nozzle LEDs back to the `ready` state.
#
#           Example: add STATUS_CLEANING to the beginning of your nozzle-cleaning macro, and then STATUS_READY
#                    to the end of it to return the LEDs back to `ready` state.
#
#     5.  Feel free to change colors of each macro, create new ones if you have a need to.  The macros provided below
#         are just an example of what is possible.  If you want to try some more complex animations, you will most
#         likely have to use WLED with Moonraker and a small micro-controller (please see the LED thread for help inside
#         of the stealthburner_beta channel on Discord).
#
#####################################
#       END INSTRUCTRUCTIONS        #
#####################################


[neopixel sb_leds]
pin: PD3
#   The pin connected to the neopixel. This parameter must be provided.
chain_count: 3
#   The number of Neopixel chips that are "daisy chained" to the
#   provided pin. The default is 1 (which indicates only a single
#   Neopixel is connected to the pin).
color_order: GRBW
#   Set the pixel order required by the LED hardware. Options are GRB,
#   RGB, GRBW, or RGBW. The default is GRB.
initial_RED: 1.0
initial_GREEN: 0.0
initial_BLUE: 0.0
initial_WHITE: 0.0
#   Sets the initial LED color of the Neopixel. Each value should be
#   between 0.0 and 1.0. The WHITE option is only available on RGBW
#   LEDs. The default for each color is 0.#

# Most configuration for the macros can be done by modifying the variables in the _sb_vars macro
# at the start of this file.

##########
# MACROS #
##########

# The following status macros are available (these go inside of your macros):
#
#    STATUS_READY
#    STATUS_OFF
#    STATUS_BUSY
#    STATUS_HEATING
#    STATUS_LEVELING
#    STATUS_HOMING
#    STATUS_CLEANING
#    STATUS_MESHING
#    STATUS_CALIBRATING_Z
#
# With additional macros for basic control:
#
#    SET_NOZZLE_LEDS_ON
#    SET_LOGO_LEDS_OFF
#    SET_NOZZLE_LEDS_OFF
#
# Contributed by Voron discord users wile.e, Tetsunosuke, and etherwalker


[gcode_macro _sb_vars]
# User settings for the StealthBurner status leds. You can change the status colors and led
# configurations for the logo and nozzle here.
variable_colors: {
        'logo': { # Colors for logo states
            'busy': {'r': 0.4, 'g': 0.0, 'b': 0.0, 'w': 0.0},
            'cleaning': {'r': 0.0, 'g': 0.02, 'b': 0.5, 'w': 0.0},
            'calibrating_z': {'r': 0.8, 'g': 0., 'b': 0.35, 'w': 0.0},
            'heating': {'r': 0.3, 'g': 0.18, 'b': 0.0, 'w': 0.0},
            'homing': {'r': 0.0, 'g': 0.6, 'b': 0.2, 'w': 0.0},
            'leveling': {'r': 0.5, 'g': 0.1, 'b': 0.4, 'w': 0.0},
            'meshing': {'r': 0.2, 'g': 1.0, 'b': 0.0, 'w': 0.0},
            'off': {'r': 0.0, 'g': 0.0, 'b': 0.0, 'w': 0.0},
            'printing': {'r': 1.0, 'g': 0.0, 'b': 0.0, 'w': 0.0},
            'standby': {'r': 0.01, 'g': 0.01, 'b': 0.01, 'w': 0.1},
        },
        'nozzle': { # Colors for nozzle states
            'heating': {'r': 0.8, 'g': 0.35, 'b': 0.0, 'w':0.0},
            'off': {'r': 0.0, 'g': 0.0, 'b': 0.0, 'w': 0.0},
            'on': {'r': 0.8, 'g': 0.8, 'b': 0.8, 'w':1.0},
            'standby': {'r': 0.6, 'g': 0.0, 'b': 0.0, 'w':0.0},
        },
        'thermal': {
            'hot': {'r': 1.0, 'g': 0.0, 'b': 0.0, 'w': 0.0},
            'cold': {'r': 0.3, 'g': 0.0, 'b': 0.3, 'w': 0.0}
        }
    }
variable_logo_led_name:         "sb_leds" 
# The name of the addressable LED chain that contains the logo LED(s)
variable_logo_idx:              "1" 
# A comma-separated list of indexes LEDs in the logo
variable_nozzle_led_name:       "sb_leds"
# The name of the addressable LED chain that contains the nozzle LED(s). This will
# typically be the same LED chain as the logo.
variable_nozzle_idx:            "2,3"
# A comma-separated list of indexes of LEDs in the nozzle
gcode:
    # This section is required.  Do Not Delete.


[gcode_macro _set_sb_leds]
gcode:
    {% set red = params.RED|default(0)|float %}
    {% set green = params.GREEN|default(0)|float %}
    {% set blue = params.BLUE|default(0)|float %}
    {% set white = params.WHITE|default(0)|float %}
    {% set led = params.LED|string %}
    {% set idx = (params.IDX|string).split(',') %}
    {% set transmit_last = params.TRANSMIT|default(1) %}

    {% for led_index in idx %}
        {% set transmit=transmit_last if loop.last else 0 %}
        set_led led={led} red={red} green={green} blue={blue} white={white} index={led_index} transmit={transmit}
    {% endfor %}

[gcode_macro _set_sb_leds_by_name]
gcode:
    {% set leds_name = params.LEDS %}
    {% set color_name = params.COLOR %}
    {% set color = printer["gcode_macro _sb_vars"].colors[leds_name][color_name] %}
    {% set led = printer["gcode_macro _sb_vars"][leds_name + "_led_name"] %}
    {% set idx = printer["gcode_macro _sb_vars"][leds_name + "_idx"] %}
    {% set transmit = params.TRANSMIT|default(1) %}

    _set_sb_leds led={led} red={color.r} green={color.g} blue={color.b} white={color.w} idx="{idx}" transmit={transmit}

[gcode_macro _set_logo_leds]
gcode:
    {% set red = params.RED|default(0)|float %}
    {% set green = params.GREEN|default(0)|float %}
    {% set blue = params.BLUE|default(0)|float %}
    {% set white = params.WHITE|default(0)|float %}
    {% set led = printer["gcode_macro _sb_vars"].logo_led_name %}
    {% set idx = printer["gcode_macro _sb_vars"].logo_idx %}
    {% set transmit=params.TRANSMIT|default(1) %}

    _set_sb_leds led={led} red={red} green={green} blue={blue} white={white} idx="{idx}" transmit={transmit}

[gcode_macro _set_nozzle_leds]
gcode:
    {% set red = params.RED|default(0)|float %}
    {% set green = params.GREEN|default(0)|float %}
    {% set blue = params.BLUE|default(0)|float %}
    {% set white = params.WHITE|default(0)|float %}
    {% set led = printer["gcode_macro _sb_vars"].nozzle_led_name %}
    {% set idx = printer["gcode_macro _sb_vars"].nozzle_idx %}
    {% set transmit=params.TRANSMIT|default(1) %}

    _set_sb_leds led={led} red={red} green={green} blue={blue} white={white} idx="{idx}" transmit={transmit}

[gcode_macro set_logo_leds_off]
gcode:
    {% set transmit=params.TRANSMIT|default(1) %}
    _set_logo_leds red=0 blue=0 green=0 white=0 transmit={transmit}

[gcode_macro set_nozzle_leds_on]
gcode:
    {% set transmit=params.TRANSMIT|default(1) %}
    _set_sb_leds_by_name leds="nozzle" color="on" transmit={transmit}
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

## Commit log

2021-11-20 new design for V2.4 300x300
    [Voron Plate 300x300 Universal v2.f3d, Voron Plate 300x300 v2.4.f3d]
2022-01-23 structure change
    [Voron Plate 250x250 Universal v2.f3d, Voron Plate 250x250 v2.4.f3d, Voron Plate 300x300 Universal v2.f3d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]
2022-05-29 stl files
    [MGN9_rail_guide_x2.stl, [a]_MGN12_rail_guide_x2.stl, [a]_belt_tensioner_a_x2.stl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]
2022-06-10 wireharness structure
2022-06-10 ínitial BOM
    [door_handle_a_x2.stl, door_handle_b_x2.stl, door_latch_x2.stl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]
2022-09-13 Updates manuals
    [fluidd.cfg, leds.cfg, menu_bed.cfg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]
2022-09-13 Adds Slicer and Test Prints data
    [Filament_Card.stl, Filament_Card_Caddy_25.stl, Heatset_Practice.stl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]
2022-09-13 adds more documentation
    [DuoCartridgeLid.step, Duo_Cartridge_LID.stl, Duo_Plenum_Lid.step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]
2022-09-13 Updates manual
    [Hinges.f3d, Microswitch_Edge_Pod.step, Microswitch_Edge_Pod.stl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]
2022-09-15 updates configs
    [fluidd.cfg, mainsail.cfg, printer.cfg]
2022-09-19 updates config
    [leds.cfg, printer.cfg, stealthburner_leds.cfg]
2022-09-25 improved config and manual
    [printer.cfg]
2022-09-30 updates config to match latest kits
    [printer.cfg]
2022-10-02 improvements to manual
    [printer.cfg]
2023-02-02 panel stls
    [bottom_panel_clip_x4.stl, bottom_panel_hinge_x2.stl, bp_corner_clip_5mm_x4.stl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]
